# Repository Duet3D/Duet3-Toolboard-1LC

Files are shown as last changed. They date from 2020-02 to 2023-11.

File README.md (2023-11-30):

# Duet-3-Toolboard-1LC
Hardware information for the Duet 3 Toolboard 1LC. This is a CAN-FD connected expansion board for Duet 3 Mainboards:[Duet 3 6HC](https://www.duet3d.com/Duet3Mainboard6HC), [Duet 3 Mini 5+](https://www.duet3d.com/duet3mini5plus) or [Duet 3 6XD](https://www.duet3d.com/duet3mainboard6xd) that is designed to provide complete control for a direct drive extruder. 

Image of Duet 3 Toolboard 1LC

Product page is here: https://www.duet3d.com/Duet3Toolboard1LC

Documentation is here: https://docs.duet3d.com/en/Duet3D_hardware/Duet_3_family/Duet_3_Toolboard_1LC

As always please discuss this on the Duet3d forum: https://forum.duet3d.com/

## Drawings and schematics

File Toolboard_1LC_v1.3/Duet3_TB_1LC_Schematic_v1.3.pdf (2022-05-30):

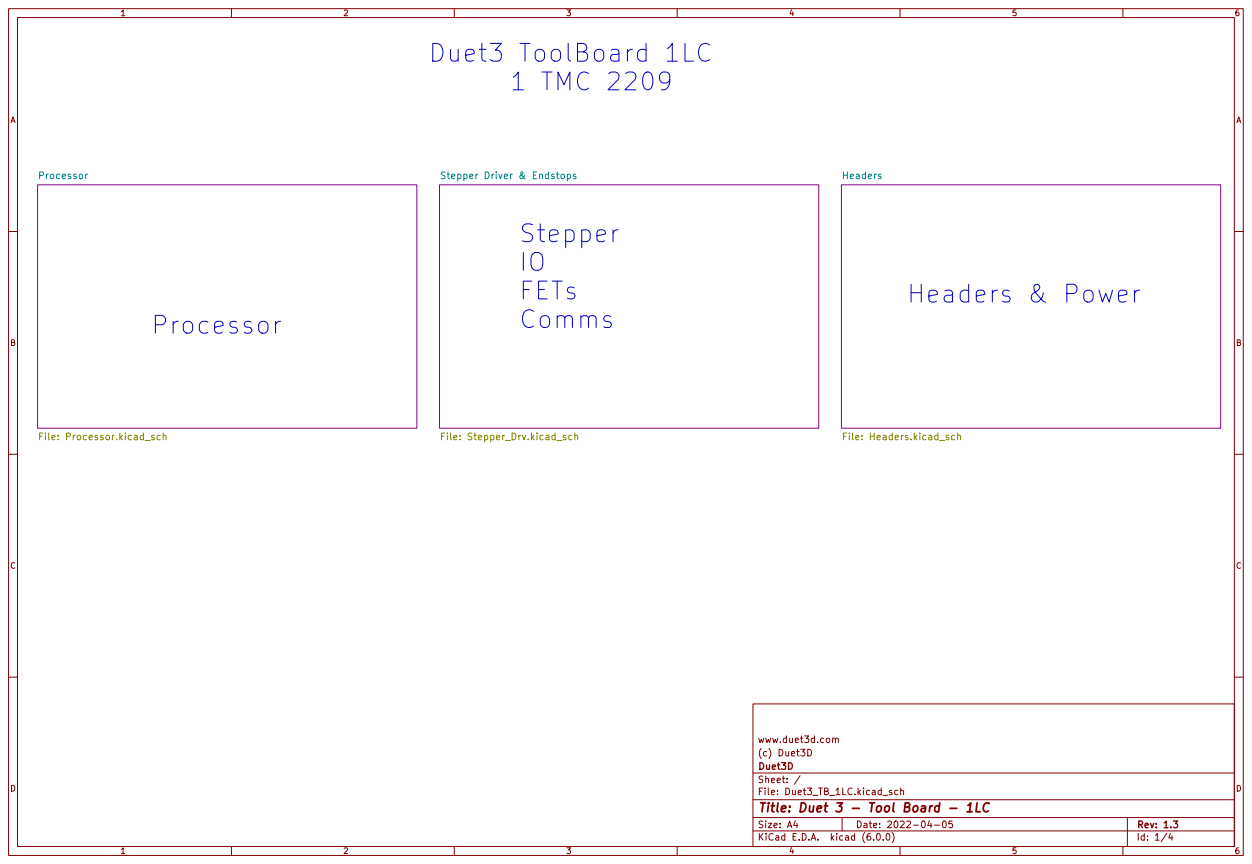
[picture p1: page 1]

Id: 1/4 Title: Duet 3 - Tool Board - 1LC

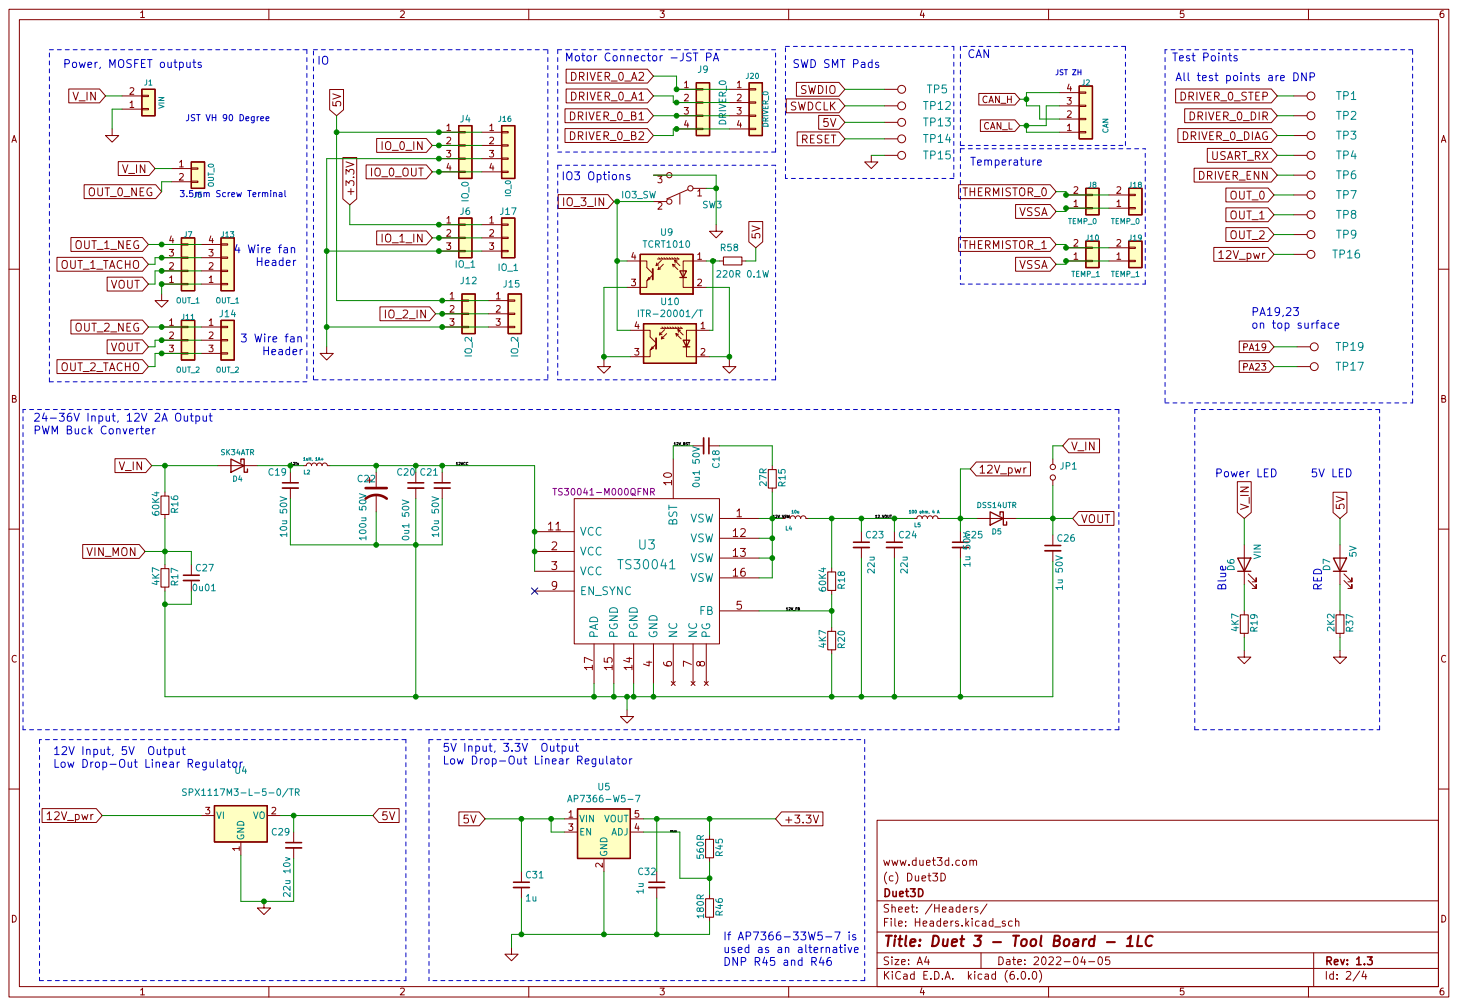
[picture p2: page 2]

12V Input, 5V Output
Low Drop-Out Linear Regulator

5V Input, 3.3V Output

www.duet3d.com
(c) Duet3D
File: Headers.kicad_sch Sheet: /Headers/ Duet3D

Id: 2/4 Title: Duet 3 - Tool Board - 1LC

If AP7366-33W5-7 is used as an alternative DNP R45 and R46

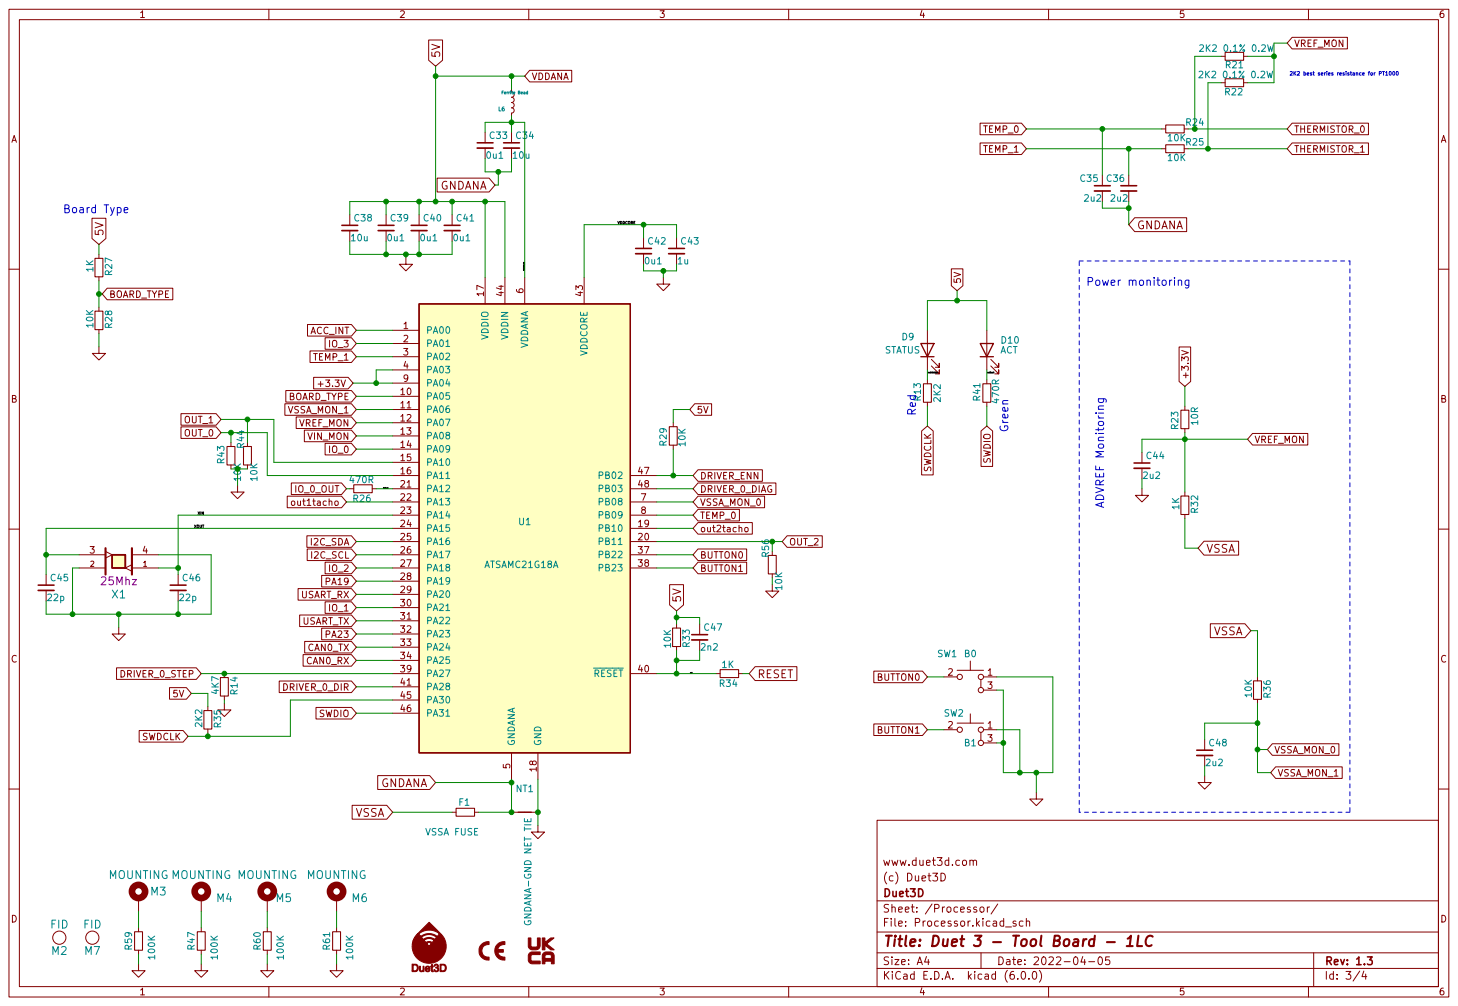
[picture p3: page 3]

2K2 best series resistance for PT1000 ADVREF Monitoring

www.duet3d.com
(c) Duet3D
File: Processor.kicad_sch Sheet: /Processor/ Duet3D

Id: 3/4 Title: Duet 3 - Tool Board - 1LC

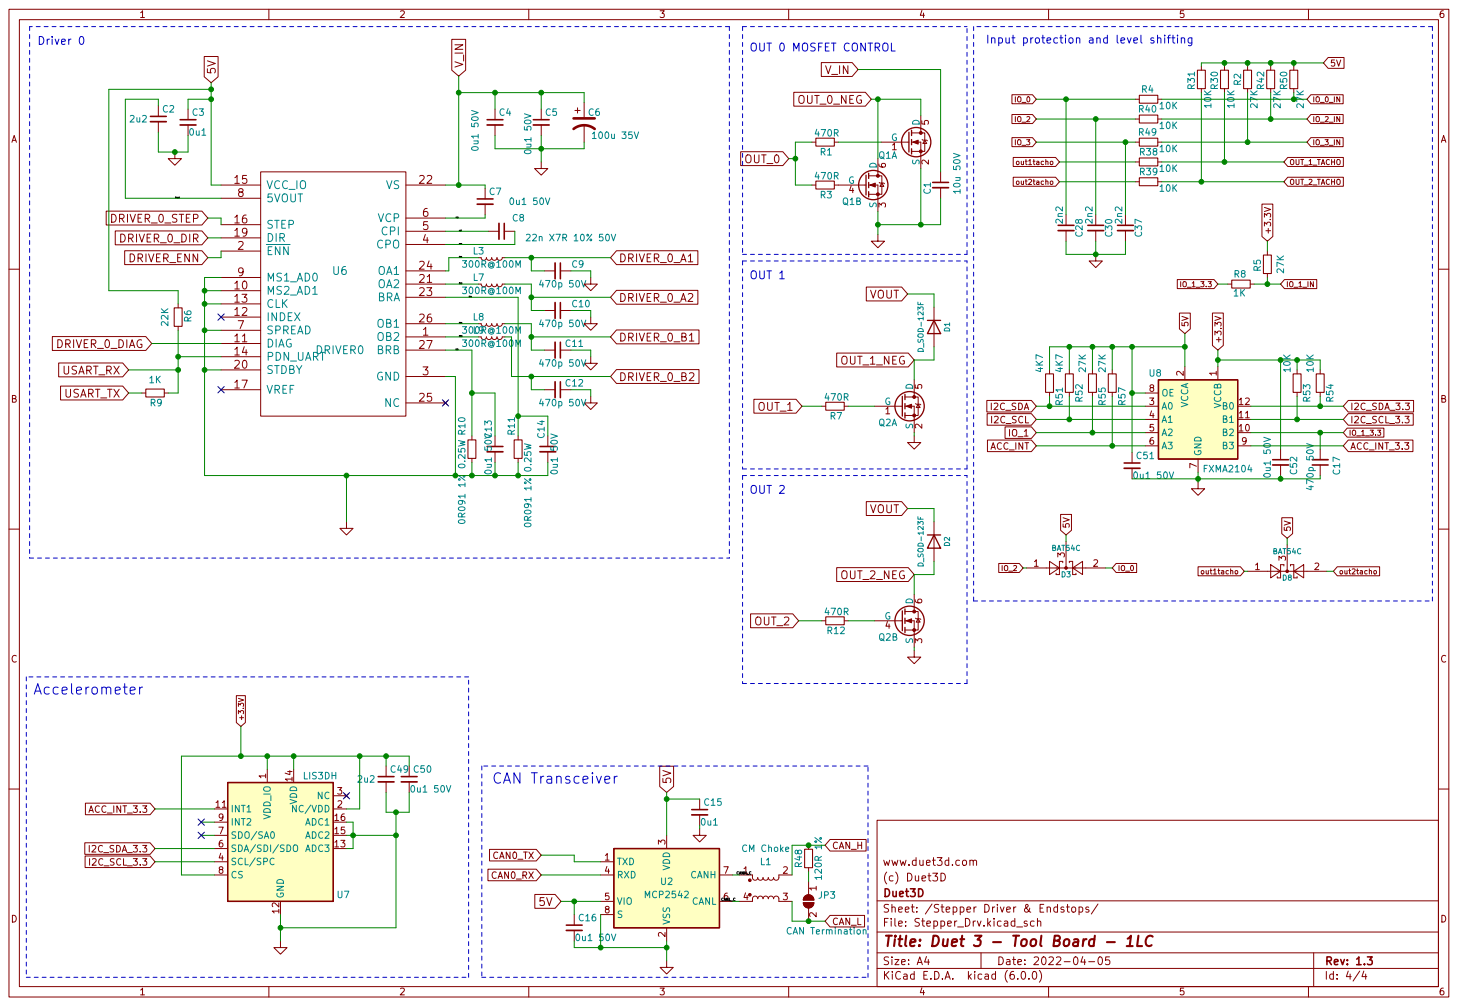
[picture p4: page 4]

Input protection and level shifting

3 RXD 4 VIO 5 CANL 6 CANH 7 S

(c) Duet3D
Sheet: /Stepper Driver & Endstops/ Duet3D

File: Stepper_Drv.kicad_sch
Id: 4/4 Title: Duet 3 - Tool Board - 1LC

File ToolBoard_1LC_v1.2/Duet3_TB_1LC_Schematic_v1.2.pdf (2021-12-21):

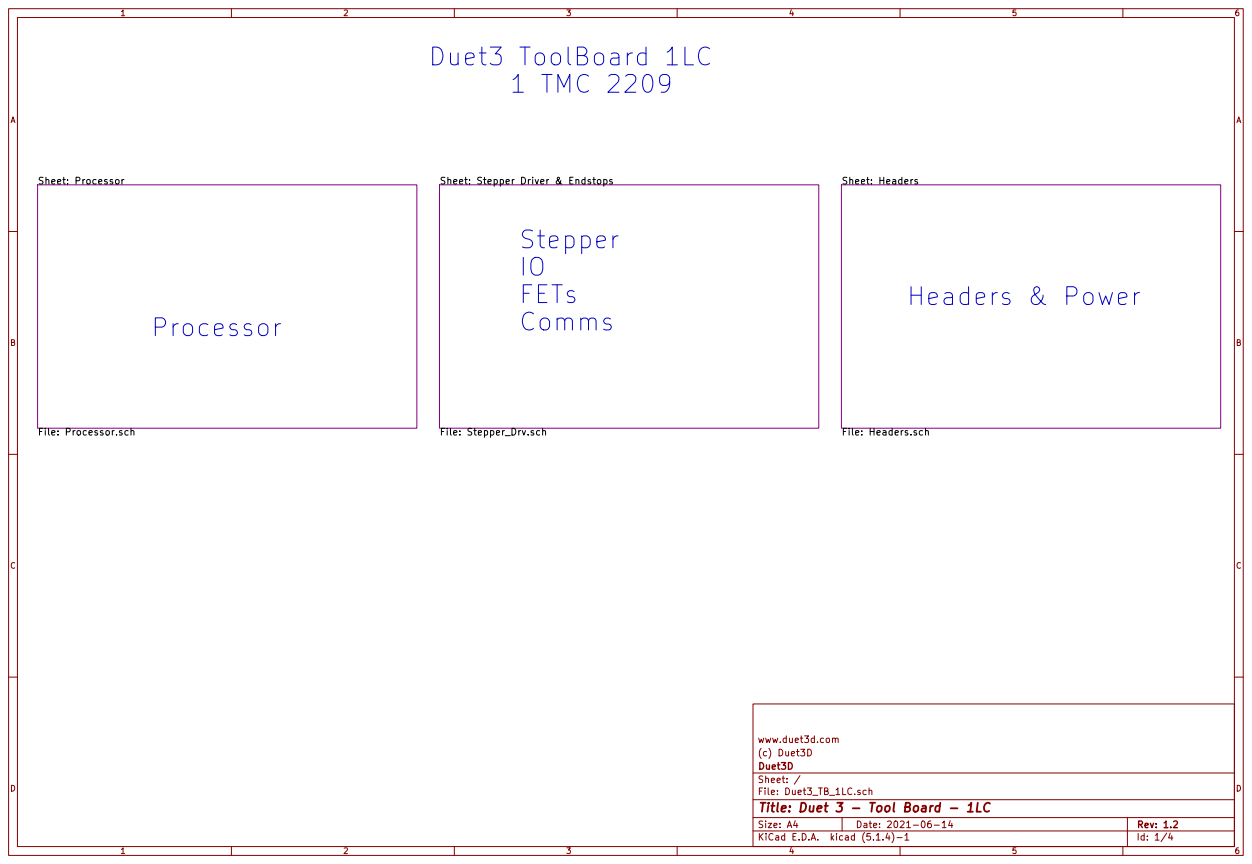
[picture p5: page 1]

Id: 1/4 Title: Duet 3 - Tool Board - 1LC

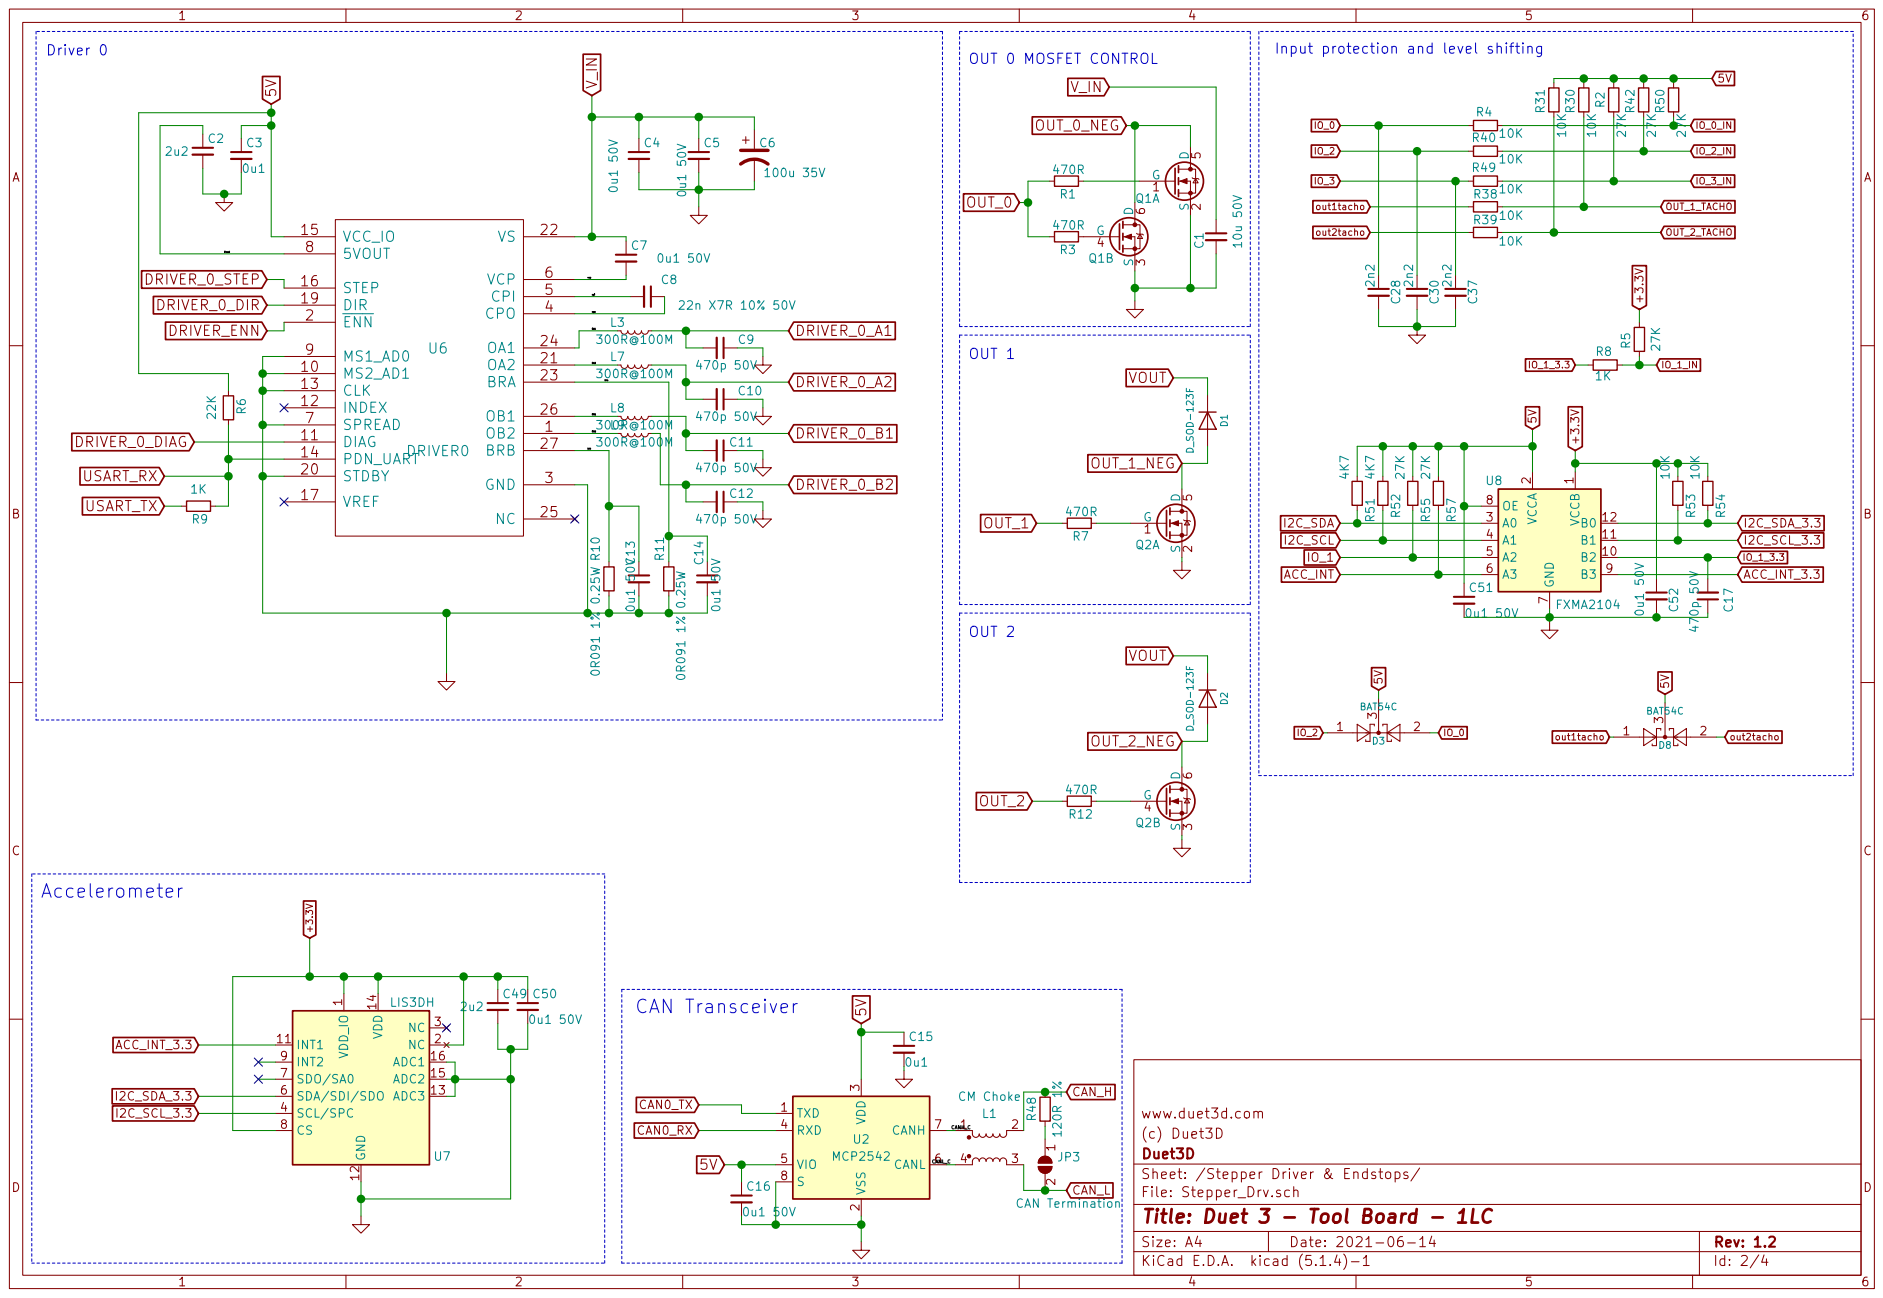
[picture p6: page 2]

3 RXD 4 VIO 5 CANL 6 CANH 7 S

(c) Duet3D
Sheet: /Stepper Driver & Endstops/ Duet3D

File: Stepper_Drv.sch
Id: 2/4 Title: Duet 3 - Tool Board - 1LC

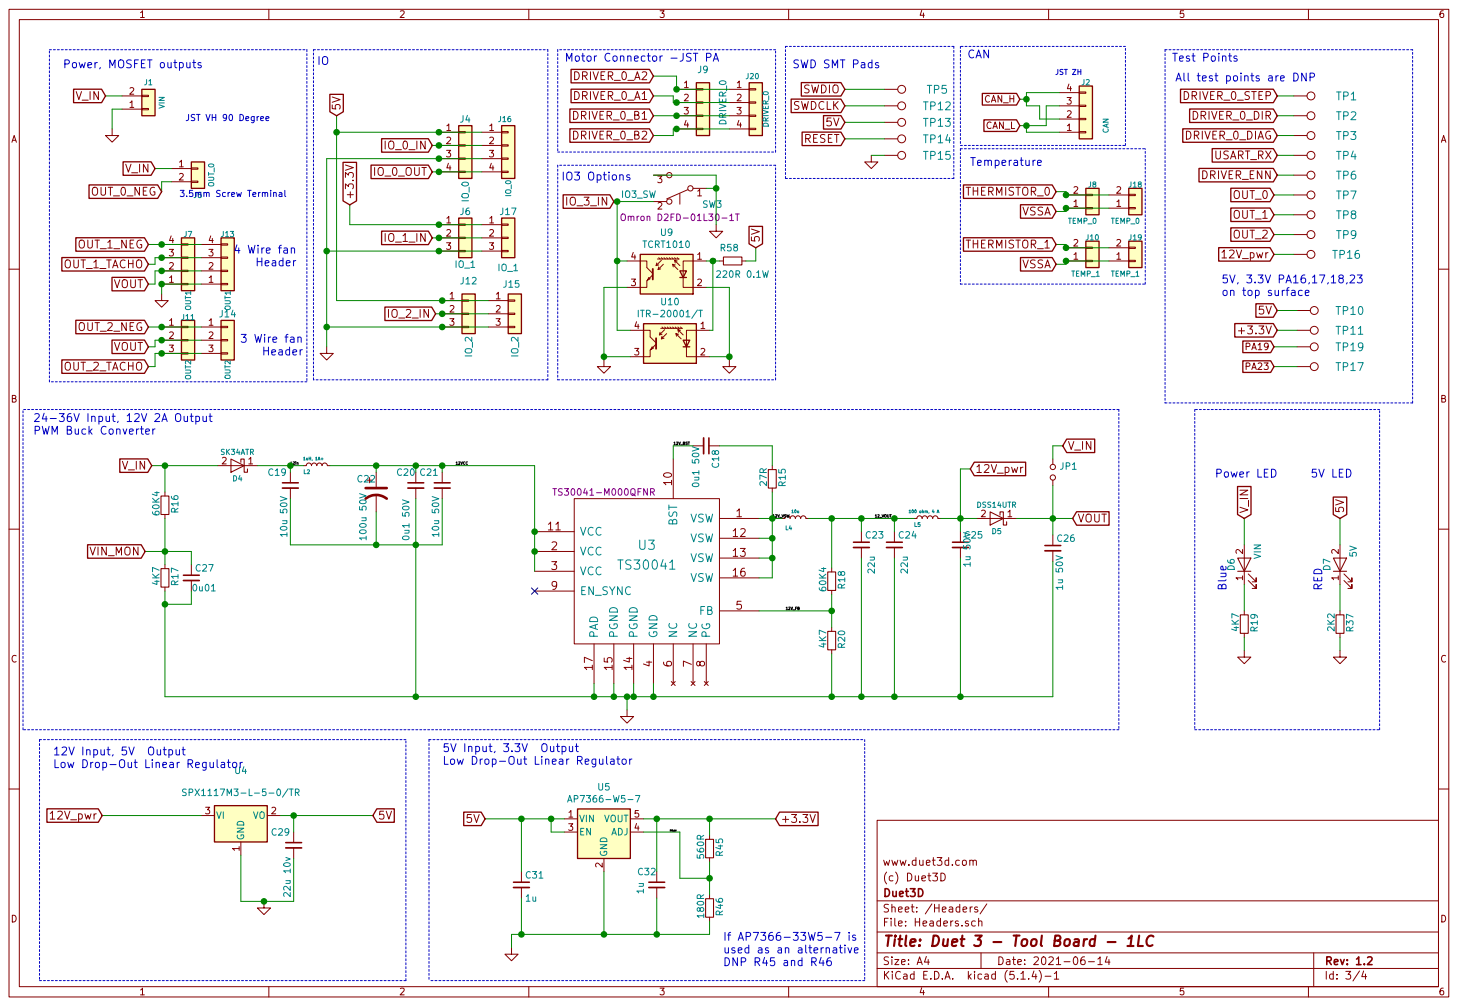
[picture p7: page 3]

12V Input, 5V Output
Low Drop-Out Linear Regulator

5V Input, 3.3V Output

www.duet3d.com
(c) Duet3D
File: Headers.sch Sheet: /Headers/ Duet3D

Id: 3/4 Title: Duet 3 - Tool Board - 1LC

If AP7366-33W5-7 is used as an alternative DNP R45 and R46

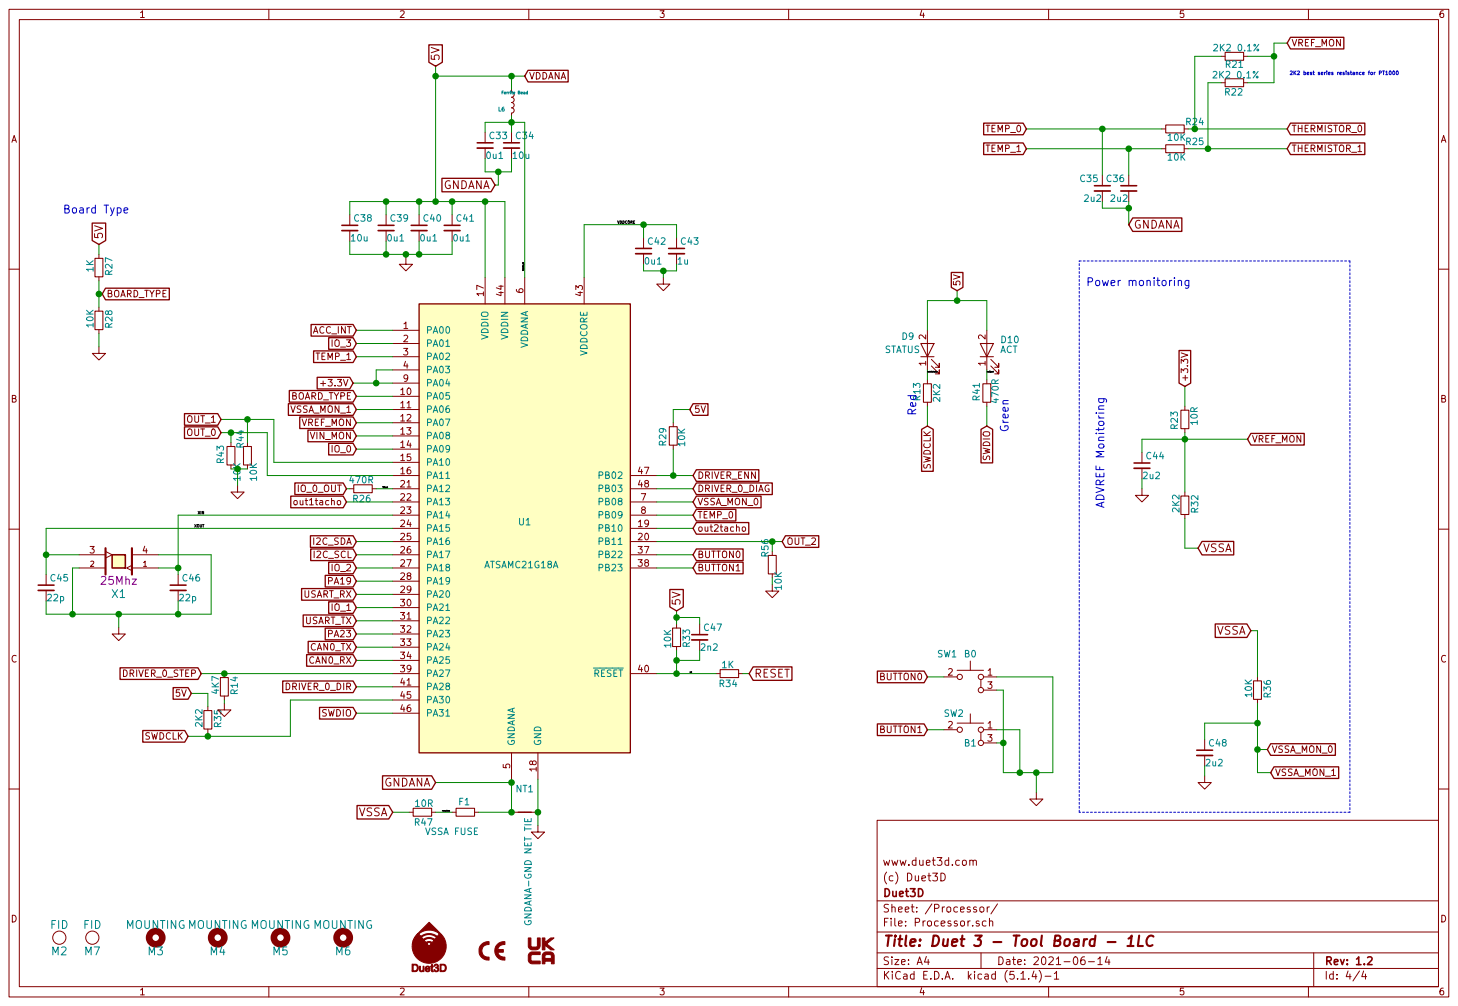
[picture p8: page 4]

www.duet3d.com
(c) Duet3D
File: Processor.sch Sheet: /Processor/ Duet3D

Id: 4/4 Title: Duet 3 - Tool Board - 1LC

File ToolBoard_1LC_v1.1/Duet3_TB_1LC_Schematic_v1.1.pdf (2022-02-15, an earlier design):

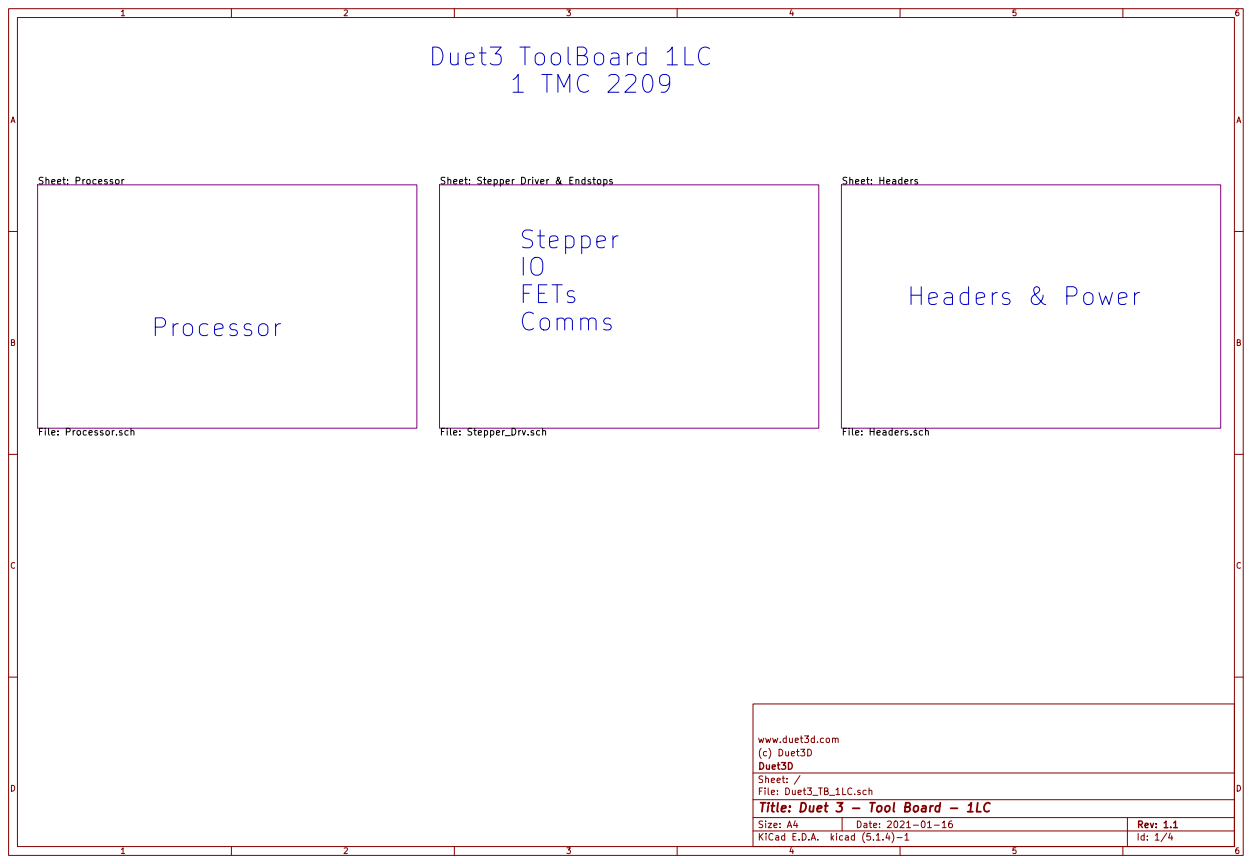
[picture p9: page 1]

Id: 1/4 Title: Duet 3 - Tool Board - 1LC

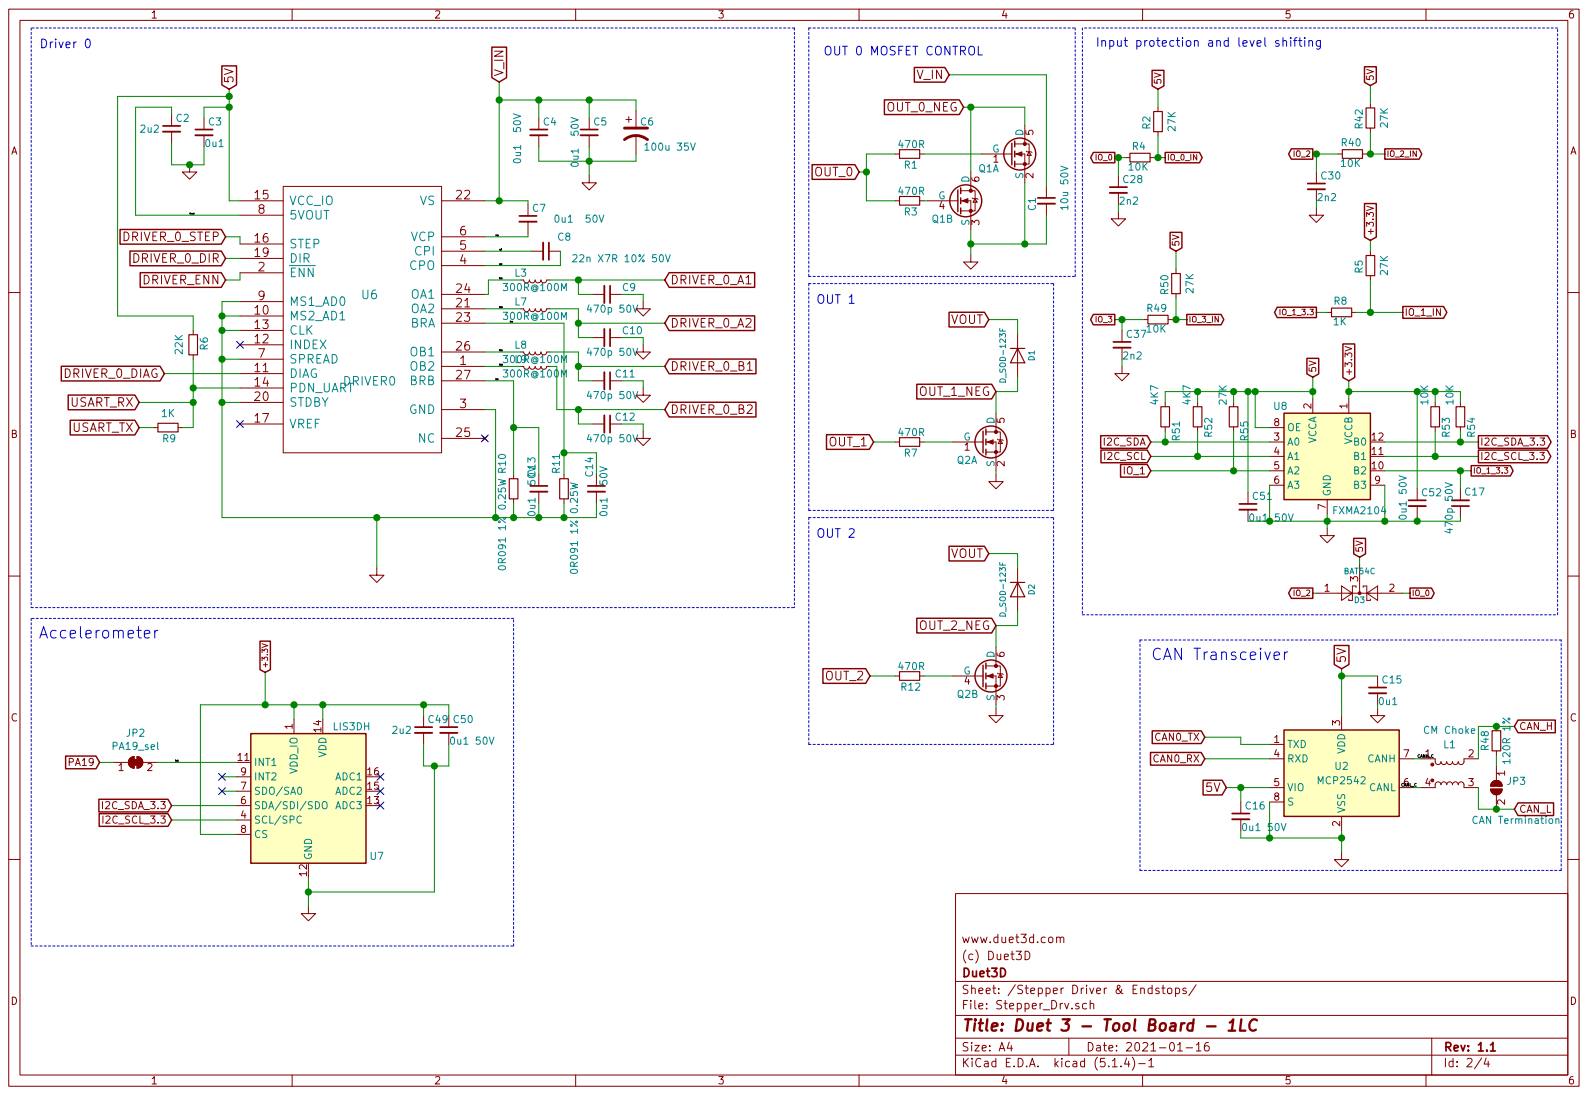
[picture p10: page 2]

CAN Transceiver

LIS3DH

3 RXD 4 VIO 5 CANL 6 CANH 7 S

(c) Duet3D
Sheet: /Stepper Driver & Endstops/ Duet3D

File: Stepper_Drv.sch
Id: 2/4 Title: Duet 3 - Tool Board - 1LC

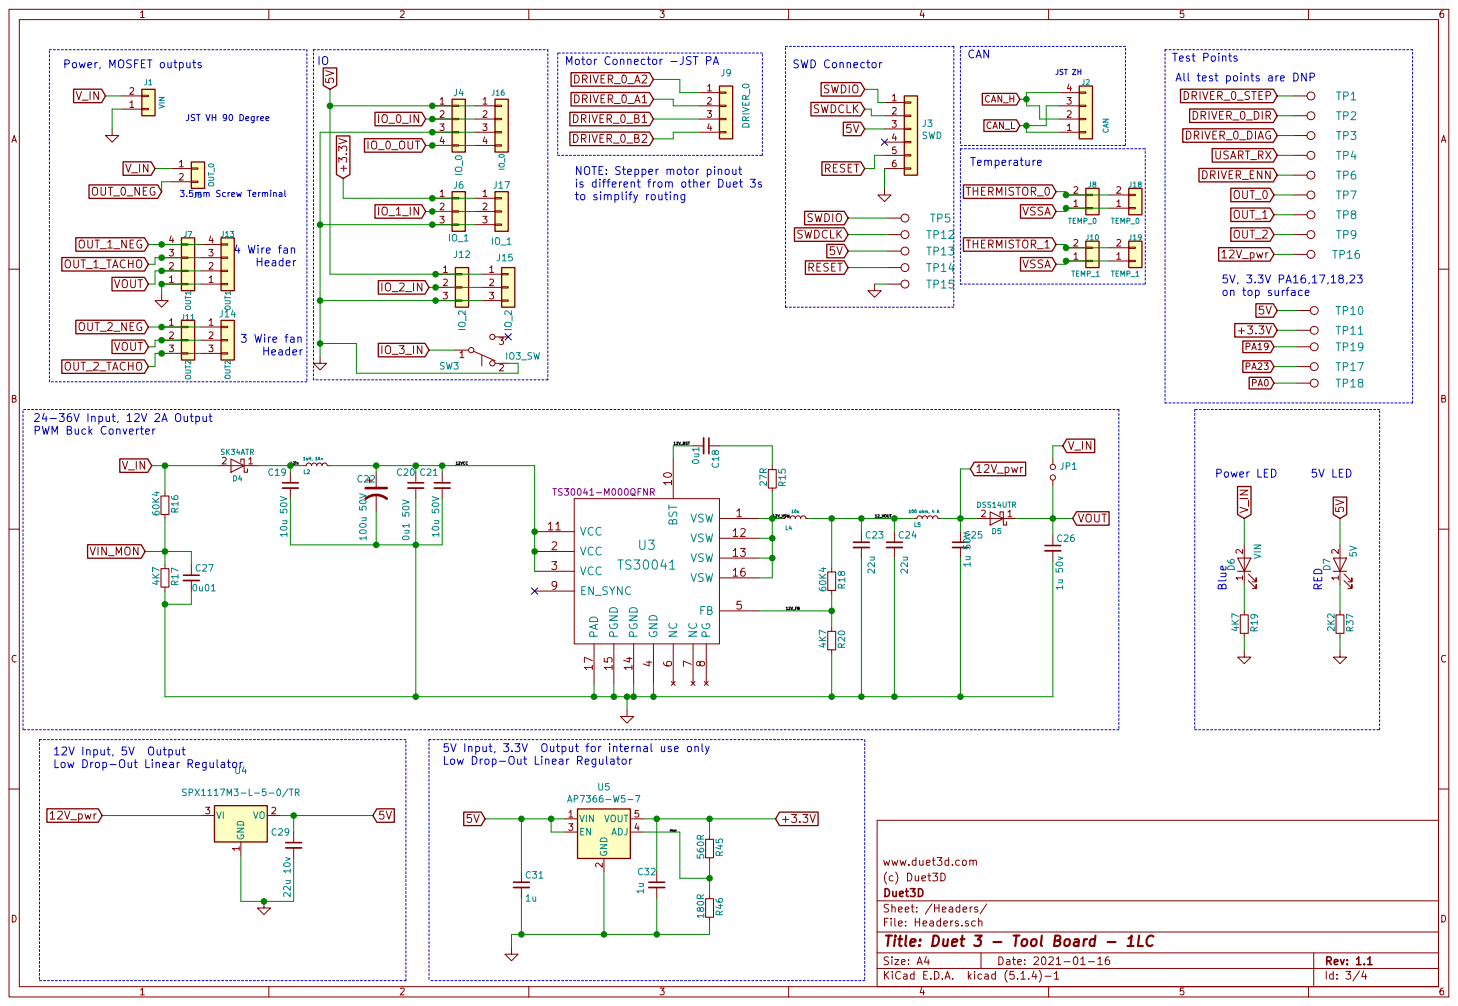
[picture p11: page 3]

is different from other Duet 3s
to simplify routing

3 Wire fan Header 3.5mm Screw Terminal 24-36V Input, 12V 2A Output

5V Input, 3.3V Output for internal use only

1 VO 2 VI 3 U4 SPX1117M3-L-5-0/TR 180R R46 VIN 1 GND

www.duet3d.com
(c) Duet3D
File: Headers.sch Sheet: /Headers/ Duet3D

Id: 3/4 Title: Duet 3 - Tool Board - 1LC

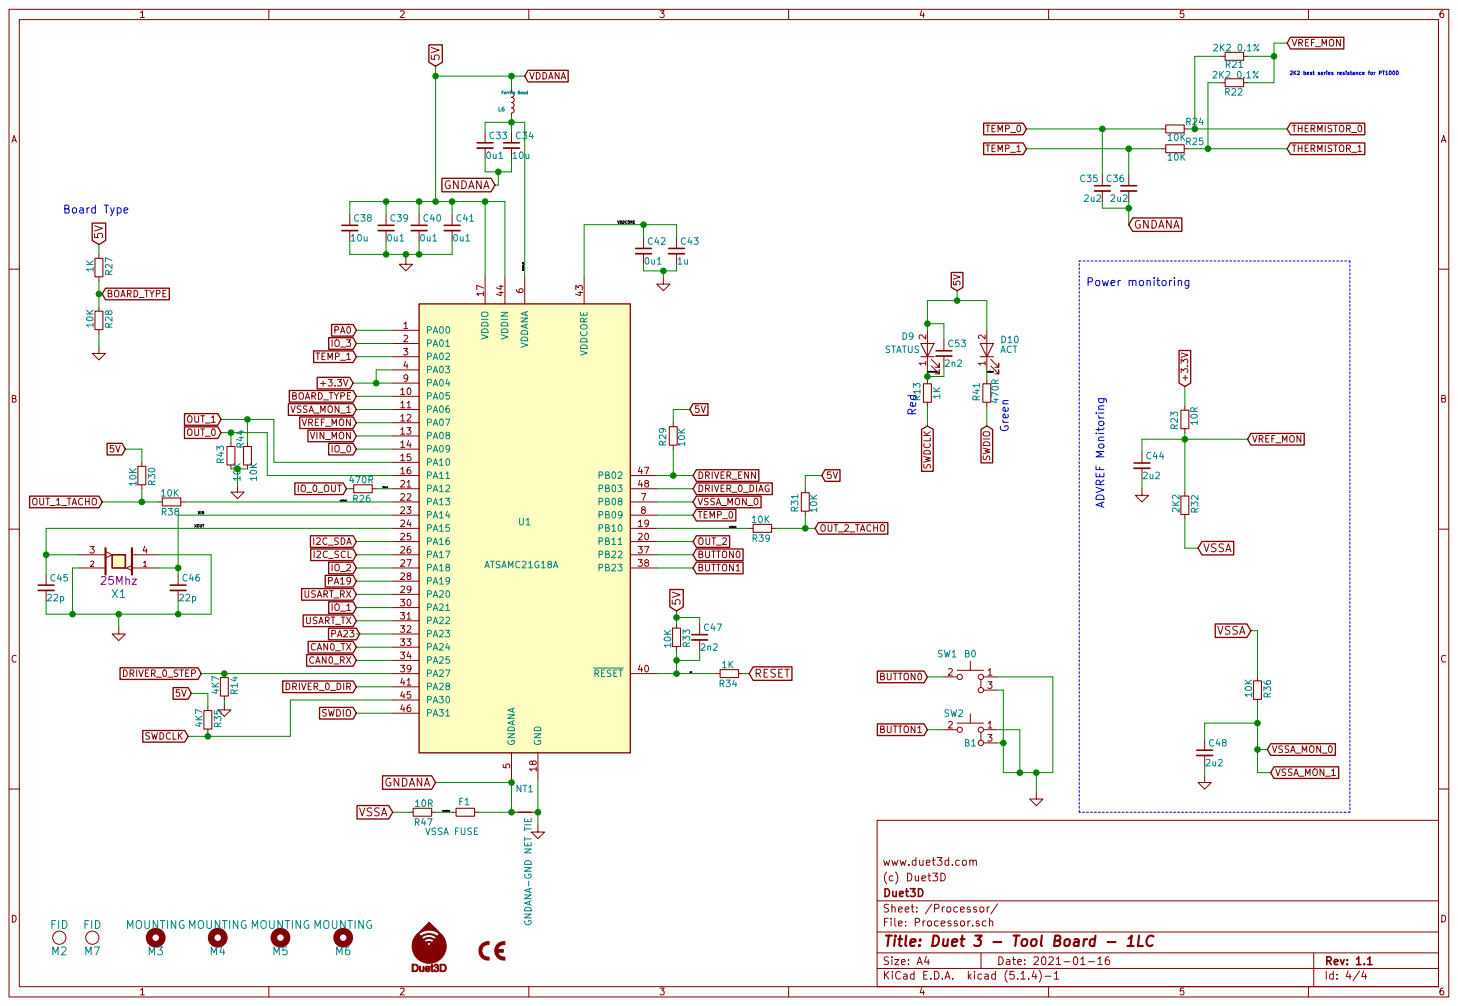
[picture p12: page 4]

2K2 best series resistance for PT1000 ADVREF Monitoring

(c) Duet3D
File: Processor.sch Sheet: /Processor/ Duet3D

Id: 4/4 Title: Duet 3 - Tool Board - 1LC

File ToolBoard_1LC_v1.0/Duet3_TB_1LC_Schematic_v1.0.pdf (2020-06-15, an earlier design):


Id: 1/4 Title: Duet 3 - Tool Board - 1LC


CAN Transceiver

3 RXD 4 VIO 5 CANL 6 CANH 7 S

www.duet3d.com (c) Duet3D Sheet: /Stepper Driver & Endstops/ Duet3D

File: Stepper_Drv.sch
Id: 2/4 Title: Duet 3 - Tool Board - 1LC


All test points are DNP

NOTE: Stepper motor pinout
is different from other Duet 3s
to simplify routing

5V and 3.3V on top surface

5V Input, 3.3V Output for internal use only
Low Drop-Out Linear Regulator

www.duet3d.com
(c) Duet3D
File: Headers.sch Sheet: /Headers/ Duet3D

Id: 3/4 Title: Duet 3 - Tool Board - 1LC


2K2 best series resistance for PT1000

www.duet3d.com
(c) Duet3D
File: Processor.sch Sheet: /Processor/ Duet3D

Id: 4/4 Title: Duet 3 - Tool Board - 1LC

CE not added until tested

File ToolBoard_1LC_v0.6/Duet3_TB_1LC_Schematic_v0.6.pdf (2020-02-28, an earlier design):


License: CERN OHL v1.2 www.duet3d.com

Id: 1/4 Title: Duet 3 - Tool Board - 1LC


CAN Transceiver

3 RXD 4 VIO 5 CANL 6 CANH 7 S

License: CERN OHL v1.2 www.duet3d.com Sheet: /Stepper Driver & Endstops/ Duet3D

File: Stepper_Drv.sch
Id: 2/4 Title: Duet 3 - Tool Board - 1LC


2.54mm Screw Terminal 2.54mm Screw Terminal Power, MOSFET outputs

All test points are DNP

2.54mm Screw Terminal NOTE: Stepper motor pinout

is different from other Duet 3s
to simplify routing

12V Input, 5V Output
Low Drop-Out Linear Regulator

5V Input, 3.3V Output for internal use only

License: CERN OHL v1.2 www.duet3d.com

File: Headers.sch Sheet: /Headers/ Duet3D

Id: 3/4 Title: Duet 3 - Tool Board - 1LC


2K2 best series resistance for PT1000 Board Type

License: CERN OHL v1.2 www.duet3d.com

File: Processor.sch Sheet: /Processor/ Duet3D

Id: 4/4 Title: Duet 3 - Tool Board - 1LC

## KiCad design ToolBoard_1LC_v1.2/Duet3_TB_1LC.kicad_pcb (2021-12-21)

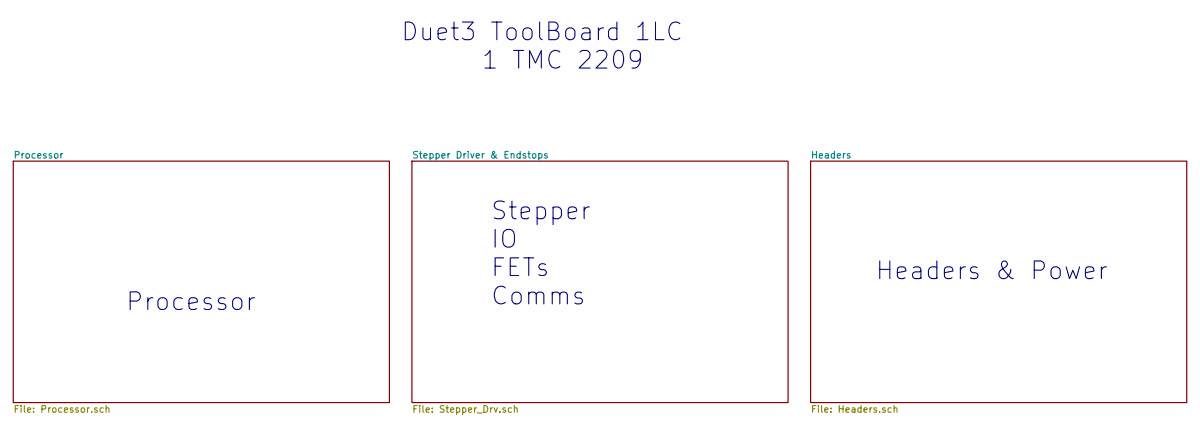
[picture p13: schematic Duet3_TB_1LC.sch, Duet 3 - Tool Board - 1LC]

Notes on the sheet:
Processor
Stepper IO FETs Comms
Headers & Power
Duet3 ToolBoard 1LC 1 TMC 2209

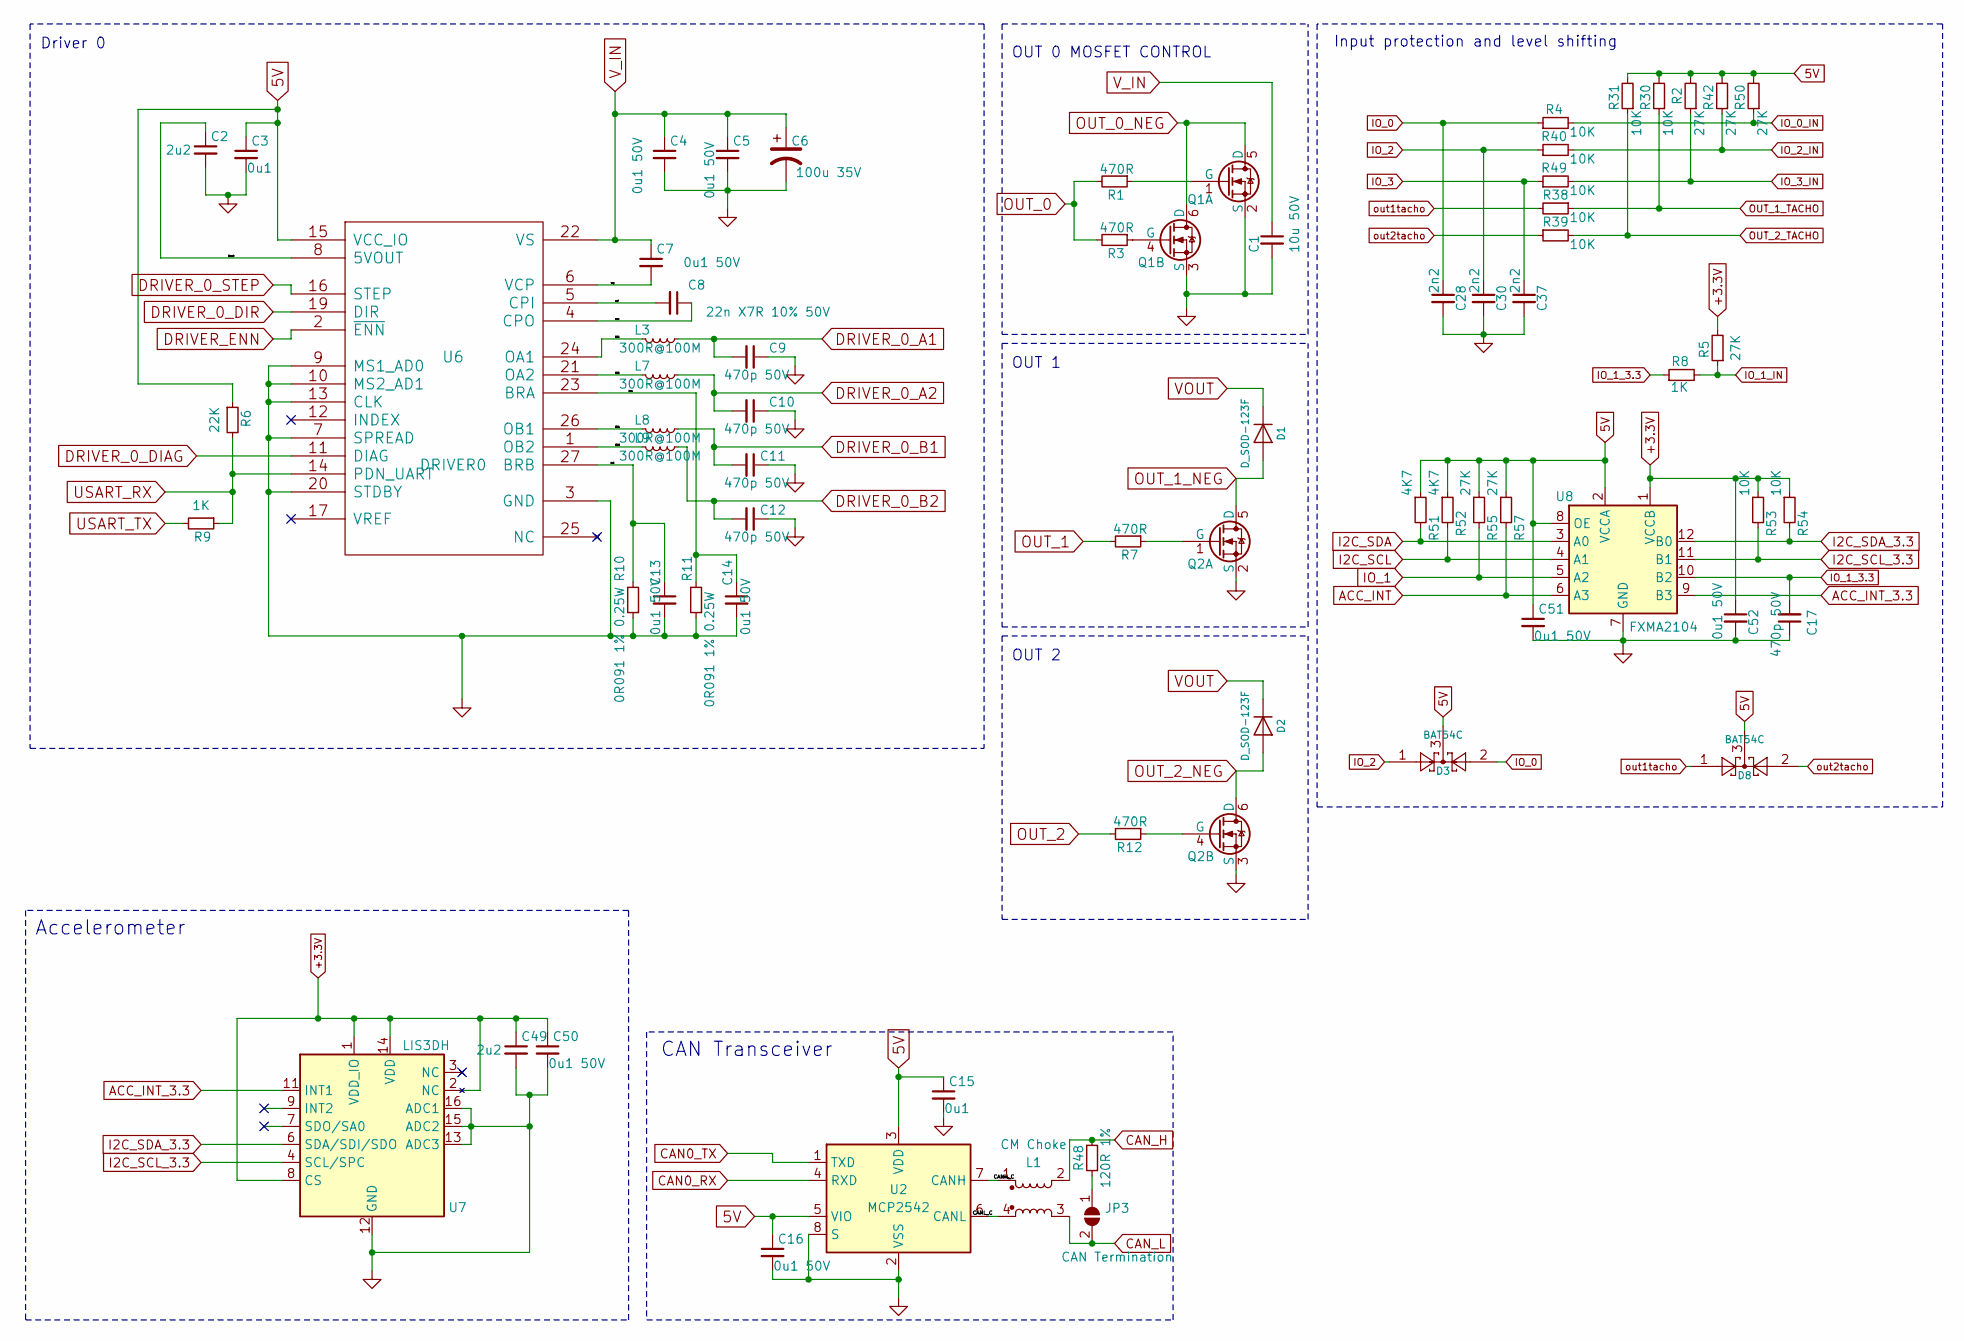
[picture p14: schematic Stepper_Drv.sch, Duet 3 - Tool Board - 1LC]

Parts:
C1: 10u 50V; C_1206_3216Metric; Part Number CL31A106KBHNNNE
C2, C49: 2u2; C_0603_1608Metric_Wbry; Part Number GRM188R6YA225KA12D
C3, C15: 0u1; C_0402_1005Metric_Wbry; Part Number CL05A104KA5NNNC
C4, C5, C7, C13, C14, C16, C50, C51, C52: 0u1 50V; C_0402_1005Metric_Wbry; Part Number GCM155R71H104KE02D
C6: 100u 35V; CP_Elec_6.3x7.7; Part Number 865080545012
C8: 22n X7R 10% 50V; C_0402_1005Metric_Wbry; Part Number CC0402KRX7R9BB223
C9, C10, C11, C12, C17: 470p 50V; C_0402_1005Metric_Wbry; Part Number CC0402KRX7R9BB471
C28, C30, C37: 2n2; C_0402_1005Metric_Wbry; Part Number CC0402KRX7R9BB222 or similar (10v+ is f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
D1, D2: D_SOD-123F; Part Number HS1KFL or equivalent
D3, D8: BAT54C; SOT-23; Part Number BAT54C-7-F/BAT54CLT1G
JP3: CAN Termination; SolderJumper-2_P1.3mm_Open_TrianglePad1.0x1.5mm
L1: CM Choke; Wurth_CM_Choke_744231121; Part Number 744231121 or SRF2012A-121YA
L3, L7, L8, L9: 300R@100M; L_0603_1608Metric; Part Number 742792641 or similar
Q1, Q2: Q_DUAL_NMOS; Fairchild_DualPower33-6_3x3mm-gap; Part Number DMT6018LDR
R1, R3, R7, R12: 470R; R_0402_1005Metric_Wbry; Part Number RK73H1ETTP4700F
R2, R5, R42, R50, R55, R57: 27K; R_0402_1005Metric_Wbry; Part Number RK73H1ETTP2702F
R4, R30, R31, R38, R39, R40, R49: 10K; R_0402_1005Metric_Wbry; Part Number RK73H1ETTP1002F
R6: 22K; R_0402_1005Metric_Wbry; Part Number RK73H1ETTP2202F
R8, R9: 1K; R_0402_1005Metric_Wbry; Part Number RK73H1ETTP1001F
R10, R11: 0R091 1% 0.25W; R_0402_1005Metric_Wbry; Part Number ERJ-2BWFR091X or RLP73M1ER091FTDF
R48: 120R 1%; R_0402_1005Metric_Wbry; Part Number RMCF0402FT120R
R51, R52: 4K7; R_0402_1005Metric_Wbry; Part Number RK73H1ETTP4701F
R53, R54: 10K; R_0402_1005Metric_Wbry; Part Number RK73H1ETTP4701F
U2: MCP2542; DFN-8-1EP_3x2mm_P0.5mm_EP1.3x1.5mm-thinpads; Part Number MCP2542, alternitivelty MCP2558
U6: DRIVER0; QFN-28-1EP_5x5mm_Pitch0.5mm-thinpads; Part Number TMC2209
U7: LIS3DH; Part Number LIS3DHTR
U8: FXMA2104; UMLP-12-1.8x1.8mm_P0.4mm

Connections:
5V: C3.1, C15.1, C16.1, C51.1, D3.3, D8.3, R2.2, R6.1, R30.2, R31.2, R42.2, R50.2, R51.1, R52.1, R55.1, R57.1, U2.3 (VDD), U2.5 (VIO), U6.15 (VCC_IO), U8.2 (VCCA), U8.8 (OE); also elsewhere on the board
+3.3V: C49.1, C50.1, C52.1, R5.2, R53.1, R54.1, U7.1 (VDD_IO), U7.2 (NC), U7.8 (CS), U7.14 (VDD), U8.1 (VCCB); also elsewhere on the board
/Stepper Driver & Endstops/5vout: C2.1, U6.8 (5VOUT)
/Stepper Driver & Endstops/CANH_C: L1.1, U2.7 (CANH)
/Stepper Driver & Endstops/CANL_C: L1.4, U2.6 (CANL)
/Stepper Driver & Endstops/OA1: L3.2, U6.24 (OA1)
/Stepper Driver & Endstops/OA2: L7.2, U6.21 (OA2)
/Stepper Driver & Endstops/OB1: L8.2, U6.26 (OB1)
/Stepper Driver & Endstops/OB2: L9.2, U6.1 (OB2)
/Stepper Driver & Endstops/bra: C14.1, R11.2, U6.23 (BRA)
/Stepper Driver & Endstops/brb: C13.1, R10.2, U6.27 (BRB)
/Stepper Driver & Endstops/cpi: C8.2, U6.5 (CPI)
/Stepper Driver & Endstops/cpo: C8.1, U6.4 (CPO)
/Stepper Driver & Endstops/vcp: C7.2, U6.6 (VCP)
ACC_INT: R57.2, U8.6 (A3); also elsewhere on the board
ACC_INT_3.3: U7.11 (INT1), U8.9 (B3)
CAN0_RX: U2.4 (RXD); also elsewhere on the board
CAN0_TX: U2.1 (TXD); also elsewhere on the board
CAN_H: L1.2, R48.2; also elsewhere on the board
CAN_L: JP3.2 (B), L1.3; also elsewhere on the board
DRIVER_0_A1: C9.2, L3.1; also elsewhere on the board
DRIVER_0_A2: C10.2, L7.1; also elsewhere on the board
DRIVER_0_B1: C11.2, L8.1; also elsewhere on the board
DRIVER_0_B2: C12.2, L9.1; also elsewhere on the board
DRIVER_0_DIAG: U6.11 (DIAG); also elsewhere on the board
DRIVER_0_DIR: U6.19 (DIR); also elsewhere on the board
DRIVER_0_STEP: U6.16 (STEP); also elsewhere on the board
DRIVER_ENN: U6.2 (~ENN); also elsewhere on the board
GND: C1.2, C2.2, C3.2, C4.2, C5.2, C6.2, C9.1, C10.1, C11.1, C12.1, C13.2, C14.2, C15.2, C16.2, C17.1, C28.2, C30.2, C37.2, C49.2, C50.2, C51.2, C52.2, Q1.2 (S), Q1.3 (S), Q2.2 (S), Q2.3 (S), R10.1, R11.1, U2.2 (VSS), U2.8 (S), U2.9 (VSS), U6.3 (GND), U6.7 (SPREAD), U6.9 (MS1_AD0), U6.10 (MS2_AD1), U6.13 (CLK), U6.18 (GND), U6.20 (STDBY), U6.29 (GND), U7.5 (GND), U7.10 (GND), U7.12 (GND), U7.13 (ADC3), U7.15 (ADC2), U7.16 (ADC1), U8.7 (GND); also elsewhere on the board
I2C_SCL: R52.2, U8.4 (A1); also elsewhere on the board
I2C_SCL_3.3: R53.2, U7.4 (SCL/SPC), U8.11 (B1)
I2C_SDA: R51.2, U8.3 (A0); also elsewhere on the board
I2C_SDA_3.3: R54.2, U7.6 (SDA/SDI/SDO), U8.12 (B0)
IO_0: C28.1, D3.2, R4.1; also elsewhere on the board
IO_0_IN: R4.2, R50.1; also elsewhere on the board
IO_1: R55.2, U8.5 (A2); also elsewhere on the board
IO_1_3.3: C17.2, R8.1, U8.10 (B2)
IO_1_IN: R5.1, R8.2; also elsewhere on the board
IO_2: C30.1, D3.1, R40.1; also elsewhere on the board
IO_2_IN: R40.2, R42.1; also elsewhere on the board
IO_3: C37.1, R49.1; also elsewhere on the board
IO_3_IN: R2.1, R49.2; also elsewhere on the board
unnamed: JP3.1 (A), R48.1
unnamed: Q1.1 (G), R1.1
unnamed: Q1.4 (G), R3.1
unnamed: Q2.1 (G), R7.1
unnamed: Q2.4 (G), R12.1
OUT_0: R1.2, R3.2; also elsewhere on the board
OUT_0_NEG: Q1.5 (D), Q1.6 (D); also elsewhere on the board
OUT_1: R7.2; also elsewhere on the board
OUT_1_NEG: D1.2 (A), Q2.5 (D); also elsewhere on the board
OUT_1_TACHO: R30.1, R38.1; also elsewhere on the board
OUT_2: R12.2; also elsewhere on the board
OUT_2_NEG: D2.2 (A), Q2.6 (D); also elsewhere on the board
OUT_2_TACHO: R31.1, R39.2; also elsewhere on the board
USART_RX: R6.2, R9.1, U6.14 (PDN_UART); also elsewhere on the board
USART_TX: R9.2; also elsewhere on the board
VOUT: D1.1 (K), D2.1 (K); also elsewhere on the board
V_IN: C1.1, C4.1, C5.1, C6.1, C7.1, U6.22 (VS), U6.28 (VS); also elsewhere on the board
out1tacho: D8.1, R38.2; also elsewhere on the board
out2tacho: D8.2, R39.1; also elsewhere on the board

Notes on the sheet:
Input protection and level shifting
Driver 0
OUT 1
OUT 0 MOSFET CONTROL
CAN Transceiver
OUT 2
Accelerometer

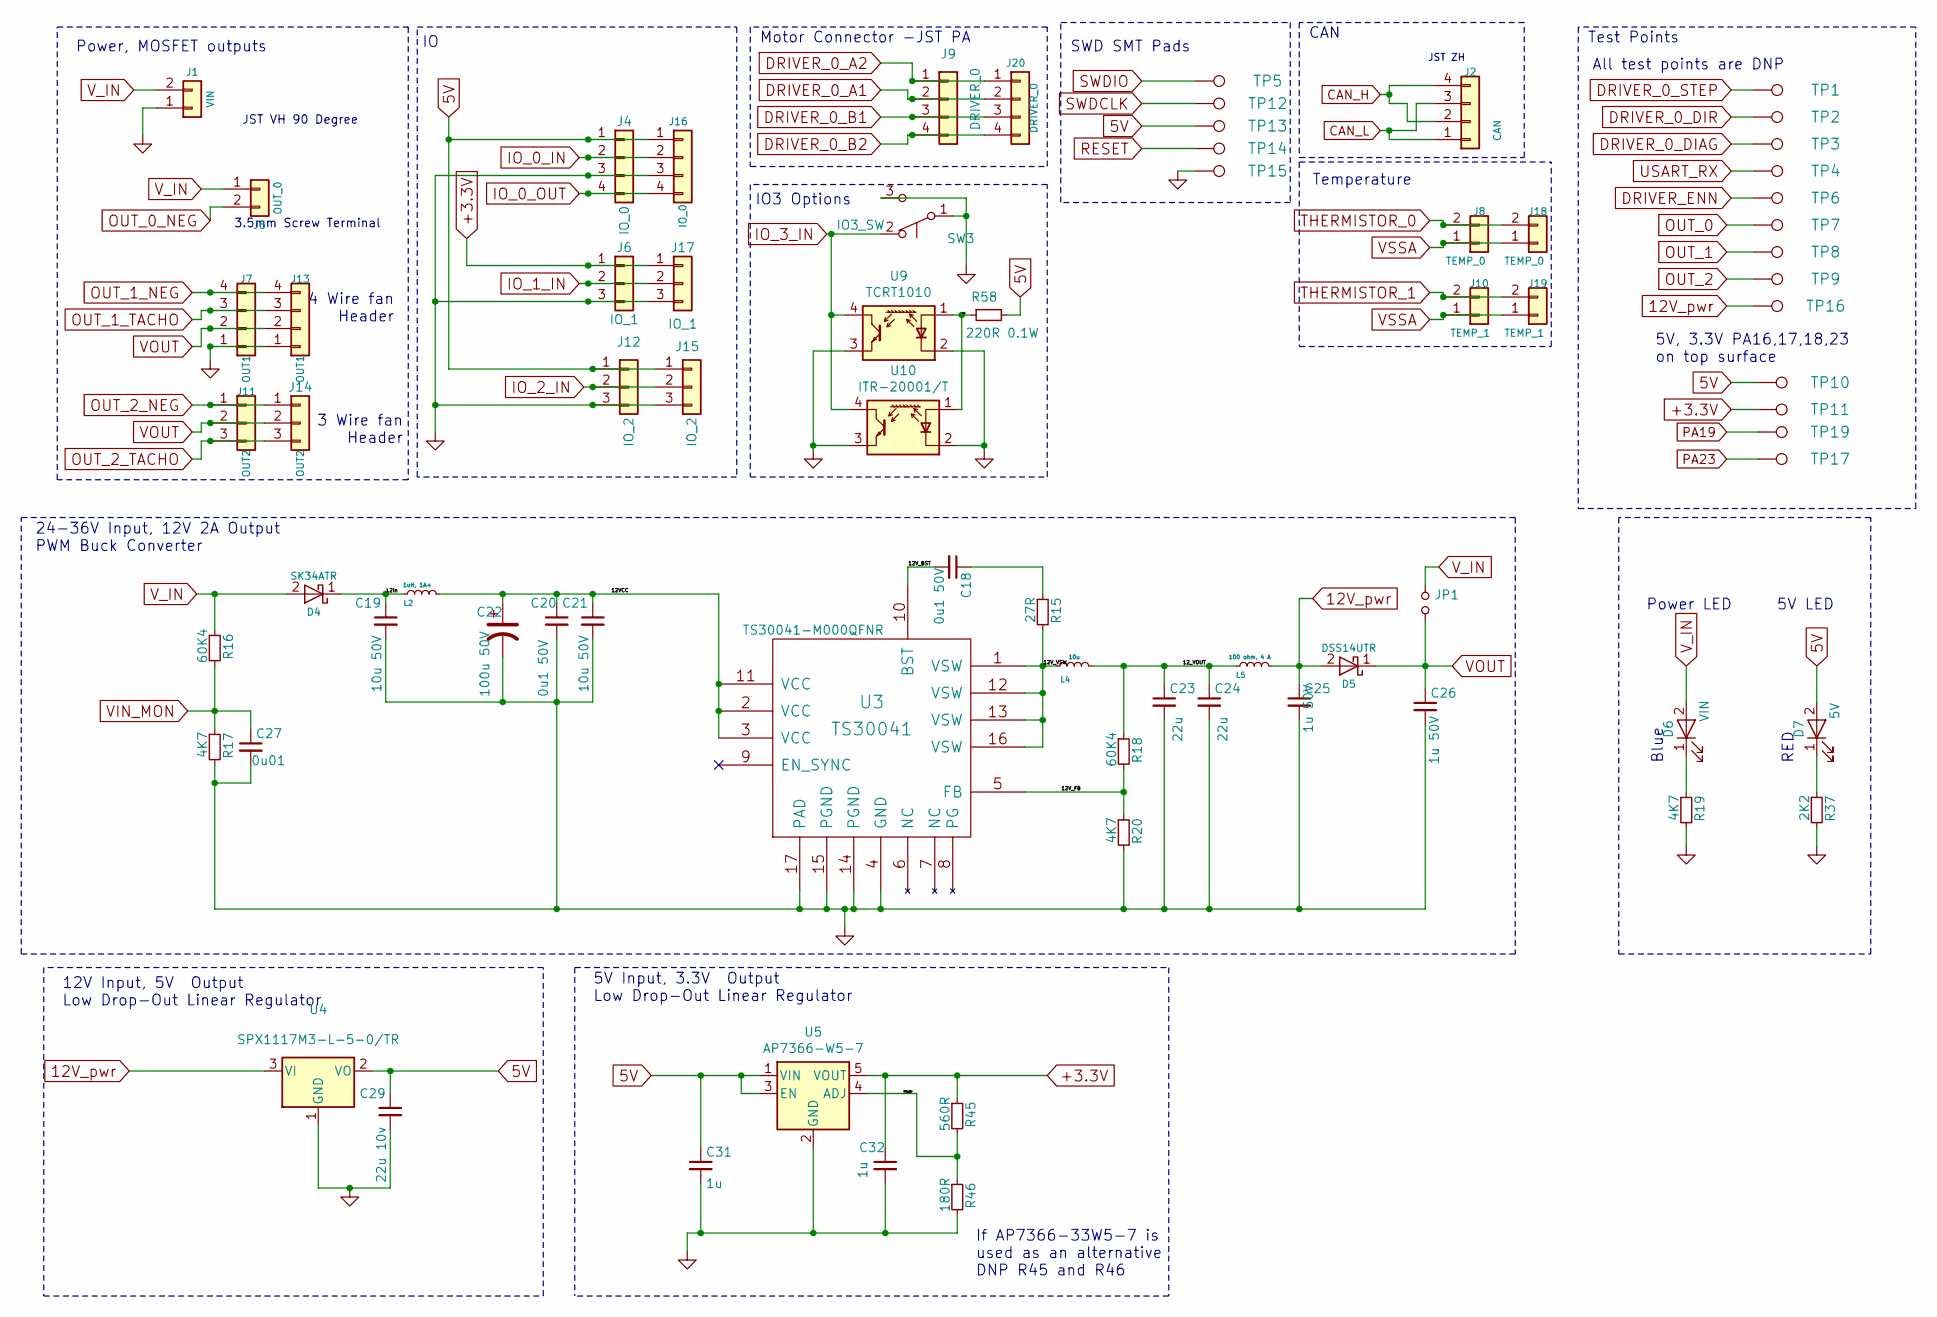
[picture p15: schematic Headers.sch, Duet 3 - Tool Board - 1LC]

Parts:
C18: 0u1 50V; C_0402_1005Metric_Wbry; Part Number CL05A104KA5NNNC
C19, C21: 10u 50V; C_1206_3216Metric; Part Number CL31A106KBHNNNE
C20: 0u1 50V; C_0402_1005Metric_Wbry; Part Number GRM155R61H104JE14D
C22: 100u 50V; CP_Elec_6.3x7.7; Part Number EEE-FTH101XAP
C23, C24: 22u; C_0805_2012Metric; Rating 25V; Part Number GRM21BR61E226ME44L
C25, C26: 1u 50V; C_0603_1608Metric_Wbry; Part Number CL10A105KB8NNNC
C27: 0u01; C_0402_1005Metric_Wbry; Part Number TMK105B7103KV-F
C29: 22u 10v; C_0805_2012Metric; Part Number GRM21BR61A226ME51L or equivalent
C31, C32: 1u; C_0603_1608Metric_Wbry; Part Number CL10A105KA8NNNC
D4: SK34ATR; D_SMA; Rating 1A+ 40V+; Part Number SK34ATR or similar SMA footprint
D5: DSS14UTR; D_SOD-123F; Rating 1A,40V; Part Number DSS14UTR or RB162MM-40TR or similar
D6: VIN; LED_0603_1608Metric; Part Number 150060BS75000 or equivalent Blue
D7: 5V; LED_0603_1608Metric; Part Number 150060RS75000 or equivalent Red
J1: VIN; JST_VH_B2PS-VH_1x02_P3.96mm_Short_Horizontal; Part Number B2PS-VH(LF)(SN)
J2: CAN; JST_ZH_S4B-ZH_1x04_P1.50mm_Horizontal; Part Number S4B-ZR(LF)(SN)
J4: IO_0; JST_PH_S4B-PH-K_1x04_P2.00mm_Horizontal; Part Number S4B-PH-K-S(LF)(SN)
J5: OUT_0; 3.5MM_2X1; Part Number Kaifeng KF128L-3.50-2
J6: IO_1; JST_PH_S3B-PH-K_1x03_P2.00mm_Horizontal; Part Number S3B-PH-K-S(LF)(SN)
J7: OUT1; JST_PH_S4B-PH-K_1x04_P2.00mm_Horizontal; Part Number S4B-PH-K-S(LF)(SN)
J8: TEMP_0; JST_PH_S2B-PH-K_1x02_P2.00mm_Horizontal; Part Number S2B-PH-K-S(LF)(SN)
J9: DRIVER_0; JST_PH_S4B-PH-K_1x04_P2.00mm_Horizontal; Part Number S4B-PH-K-S(LF)(SN)
J10: TEMP_1; JST_PH_S2B-PH-K_1x02_P2.00mm_Horizontal; Part Number S2B-PH-K-S(LF)(SN)
J11: OUT2; JST_PH_S3B-PH-K_1x03_P2.00mm_Horizontal; Part Number S3B-PH-K-S(LF)(SN)
J12: IO_2; JST_PH_S3B-PH-K_1x03_P2.00mm_Horizontal; Part Number S3B-PH-K-S(LF)(SN)
J13: OUT1; TerminalBlock_TE_282834-4_1x04_P2.54mm_Horizontal; Part Number - DNP
J14: OUT2; TerminalBlock_TE_282834-3_1x03_P2.54mm_Horizontal; Part Number - DNP
J15: IO_2; TerminalBlock_TE_282834-3_1x03_P2.54mm_Horizontal; Part Number DNP
J16: IO_0; TerminalBlock_TE_282834-4_1x04_P2.54mm_Horizontal; Part Number - DNP
J17: IO_1; TerminalBlock_TE_282834-3_1x03_P2.54mm_Horizontal; Part Number - DNP
J18: TEMP_0; TerminalBlock_Valcon_MB312-2.54-02_P2.54mm_Horizontal; Part Number MB312-2.54-02_P2.54mm - DNP
J19: TEMP_1; TerminalBlock_Valcon_MB312-2.54-02_P2.54mm_Horizontal; Part Number MB312-2.54-02_P2.54mm - DNP
J20: DRIVER_0; TerminalBlock_TE_282834-4_1x04_P2.54mm_Horizontal; Part Number - DNP
JP1: V_OUT JMP; PinHeader_1x02_P2.54mm_Vertical
L2: 1uH, 1A+; L_1008_2512Metric; Part Number MGV2520101R0M-10 or similar 1008 footpr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
L4: 10u; L_Wuerth_7440405xxxx; Part Number 74404054100 or NR5040T100M
L5: 100 ohm, 4 A; L_0805_2012Metric; Part Number MPZ2012S101A or similar
R15: 27R; R_0402_1005Metric_Wbry; Rating 0.1W+; Part Number RC0402FR-0727RL
R16, R18: 60K4; R_0402_1005Metric_Wbry; Part Number ERJ-2RKF6042X
R17, R19, R20: 4K7; R_0402_1005Metric_Wbry; Part Number RK73H1ETTP4701F
R37: 2K2; R_0402_1005Metric_Wbry; Part Number RK73H1ETTP2201F
R45: 560R; R_0402_1005Metric_Wbry; Part Number RMCF0402FT560R
R46: 180R; R_0402_1005Metric_Wbry; Part Number RMCF0402FT180R
R58: 220R 0.1W; R_0402_1005Metric_Wbry; Part Number RK73H1ETTP2200F
SW3: IO3_SW; Ultra_Subminiature_Switch-SPDT; Part Number DNP - Omron D2FD-1L30-1T
TP1: STEP; TestPoint_Pad_D1.5mm; Part Number virtual component - DNP
TP2: DIR; TestPoint_Pad_D1.5mm; Part Number virtual component - DNP
TP3: DIAG; TestPoint_Pad_D1.5mm; Part Number virtual component - DNP
TP4: U_RX; TestPoint_Pad_D1.5mm; Part Number virtual component - DNP
TP5: SWDIO; TestPoint_Pad_D1.5mm; Part Number virtual component - DNP
TP6: ENN; TestPoint_Pad_D1.5mm; Part Number virtual component - DNP
TP7: OUT_0; TestPoint_Pad_D1.5mm; Part Number virtual component - DNP
TP8: OUT_1; TestPoint_Pad_D1.5mm; Part Number virtual component - DNP
TP9: OUT_2; TestPoint_Pad_D1.5mm; Part Number virtual component - DNP
TP10, TP13: 5V; TestPoint_Pad_D1.5mm; Part Number virtual component - DNP
TP11: 3.3V; TestPoint_Pad_D1.5mm; Part Number virtual component - DNP
TP12: SWDCLK; TestPoint_Pad_D1.5mm; Part Number virtual component - DNP
TP14: RESET; TestPoint_Pad_D1.5mm; Part Number virtual component - DNP
TP15: GND; TestPoint_Pad_D1.5mm; Part Number virtual component - DNP
TP16: 12V_pwr; TestPoint_Pad_D1.5mm; Part Number virtual component - DNP
TP17: PA23; TestPoint_Pad_D1.5mm; Part Number virtual component - DNP
TP19: PA19; TestPoint_Pad_D1.5mm; Part Number virtual component - DNP
U3: TS30041; QFN-16-1EP_3x3mm_P0.5mm_EP1.8x1.8mm-thinpads; Rating Adj (set to 12V) 1A; Part Number TS30041-M000QFNR
U4: SPX1117M3-L-5-0/TR; SOT-223-3_TabPin2; Part Number SPX1117M3-L-5-0/TR
U5: AP7366-W5-7; SOT-23-5; Part Number AP7366-W5-7 (If AP7366-33W5-7 is used a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
U9: TCRT1010; Vishay_TCRT1010; Part Number DNP
U10: ITR-20001/T; ITR-20001_T; Part Number DNP

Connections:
5V: C29.1, C31.1, D7.2 (A), J4.1, J12.1, J15.1, J16.1, R58.2, TP10.1, TP13.1, U4.2 (VO), U5.1 (VIN), U5.3 (EN); also elsewhere on the board
12V_pwr: C25.1, D5.2 (A), L5.2, TP16.1, U4.3 (VI)
+3.3V: C32.1, J6.1, J17.1, R45.1, TP11.1, U5.5 (VOUT); also elsewhere on the board
/Headers/3V3_ADJ: R45.2, R46.1, U5.4 (ADJ)
/Headers/12VCC: C20.1, C21.1, C22.1, L2.2, U3.2 (VCC), U3.3 (VCC), U3.11 (VCC)
/Headers/12V_BST: C18.2, U3.10 (BST)
/Headers/12V_FB: R18.2, R20.1, U3.5 (FB)
/Headers/12V_VSW: L4.1, R15.2, U3.1 (VSW), U3.12 (VSW), U3.13 (VSW), U3.16 (VSW)
/Headers/12_VOUT: C23.1, C24.1, L4.2, L5.1, R18.1
/Headers/L2in: C19.1, D4.1 (K), L2.1
/Headers/col: R58.1, U9.1 (A), U10.1 (A)
CAN_H: J2.2, J2.4; also elsewhere on the board
CAN_L: J2.1, J2.3; also elsewhere on the board
DRIVER_0_A1: J9.2, J20.2; also elsewhere on the board
DRIVER_0_A2: J9.1, J20.1; also elsewhere on the board
DRIVER_0_B1: J9.3, J20.3; also elsewhere on the board
DRIVER_0_B2: J9.4, J20.4; also elsewhere on the board
DRIVER_0_DIAG: TP3.1; also elsewhere on the board
DRIVER_0_DIR: TP2.1; also elsewhere on the board
DRIVER_0_STEP: TP1.1; also elsewhere on the board
DRIVER_ENN: TP6.1; also elsewhere on the board
GND: C19.2, C20.2, C21.2, C22.2, C23.2, C24.2, C25.2, C26.2, C27.2, C29.2, C31.2, C32.2, J1.1, J4.3, J6.3, J7.1, J12.3, J13.1, J15.3, J16.3, J17.3, R17.2, R19.2, R20.2, R37.2, R46.2, SW3.1 (B), SW3.3 (C), TP15.1, U3.4 (GND), U3.14 (PGND), U3.15 (PGND), U3.17 (PAD), U4.1 (GND), U5.2 (GND), U9.2 (K), U9.3 (E), U10.2 (K), U10.3 (E); also elsewhere on the board
IO_0_IN: J4.2, J16.2; also elsewhere on the board
IO_0_OUT: J4.4, J16.4; also elsewhere on the board
IO_1_IN: J6.2, J17.2; also elsewhere on the board
IO_2_IN: J12.2, J15.2; also elsewhere on the board
IO_3_IN: SW3.2 (A), U9.4 (C), U10.4 (C); also elsewhere on the board
unnamed: C18.1, R15.1
unnamed: D6.1 (K), R19.1
unnamed: D7.1 (K), R37.1
OUT_0: TP7.1; also elsewhere on the board
OUT_0_NEG: J5.2; also elsewhere on the board
OUT_1: TP8.1; also elsewhere on the board
OUT_1_NEG: J7.4, J13.4; also elsewhere on the board
OUT_1_TACHO: J7.3, J13.3; also elsewhere on the board
OUT_2: TP9.1; also elsewhere on the board
OUT_2_NEG: J11.1, J14.1; also elsewhere on the board
OUT_2_TACHO: J11.3, J14.3; also elsewhere on the board
PA19: TP19.1; also elsewhere on the board
PA23: TP17.1; also elsewhere on the board
RESET: TP14.1; also elsewhere on the board
SWDCLK: TP12.1; also elsewhere on the board
SWDIO: TP5.1; also elsewhere on the board
THERMISTOR_0: J8.2, J18.2; also elsewhere on the board
THERMISTOR_1: J10.2, J19.2; also elsewhere on the board
USART_RX: TP4.1; also elsewhere on the board
VIN_MON: C27.1, R16.2, R17.1; also elsewhere on the board
VOUT: C26.1, D5.1 (K), J7.2, J11.2, J13.2, J14.2, JP1.2; also elsewhere on the board
VSSA: J8.1, J10.1, J18.1, J19.1; also elsewhere on the board
V_IN: D4.2 (A), D6.2 (A), J1.2, J5.1, JP1.1, R16.1; also elsewhere on the board

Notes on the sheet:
Power, MOSFET outputs
Temperature
Motor Connector -JST PA
Test Points
All test points are DNP
CAN
SWD SMT Pads
4 Wire fan Header
5V, 3.3V PA16,17,18,23 on top surface
5V Input, 3.3V Output Low Drop-Out Linear Regulator
Power LED
Blue
12V Input, 5V Output Low Drop-Out Linear Regulator
24-36V Input, 12V 2A Output PWM Buck Converter
3.5mm Screw Terminal
3 Wire fan Header
5V LED
RED
JST VH 90 Degree
JST ZH
IO3 Options
If AP7366-33W5-7 is used as an alternative DNP R45 and R46

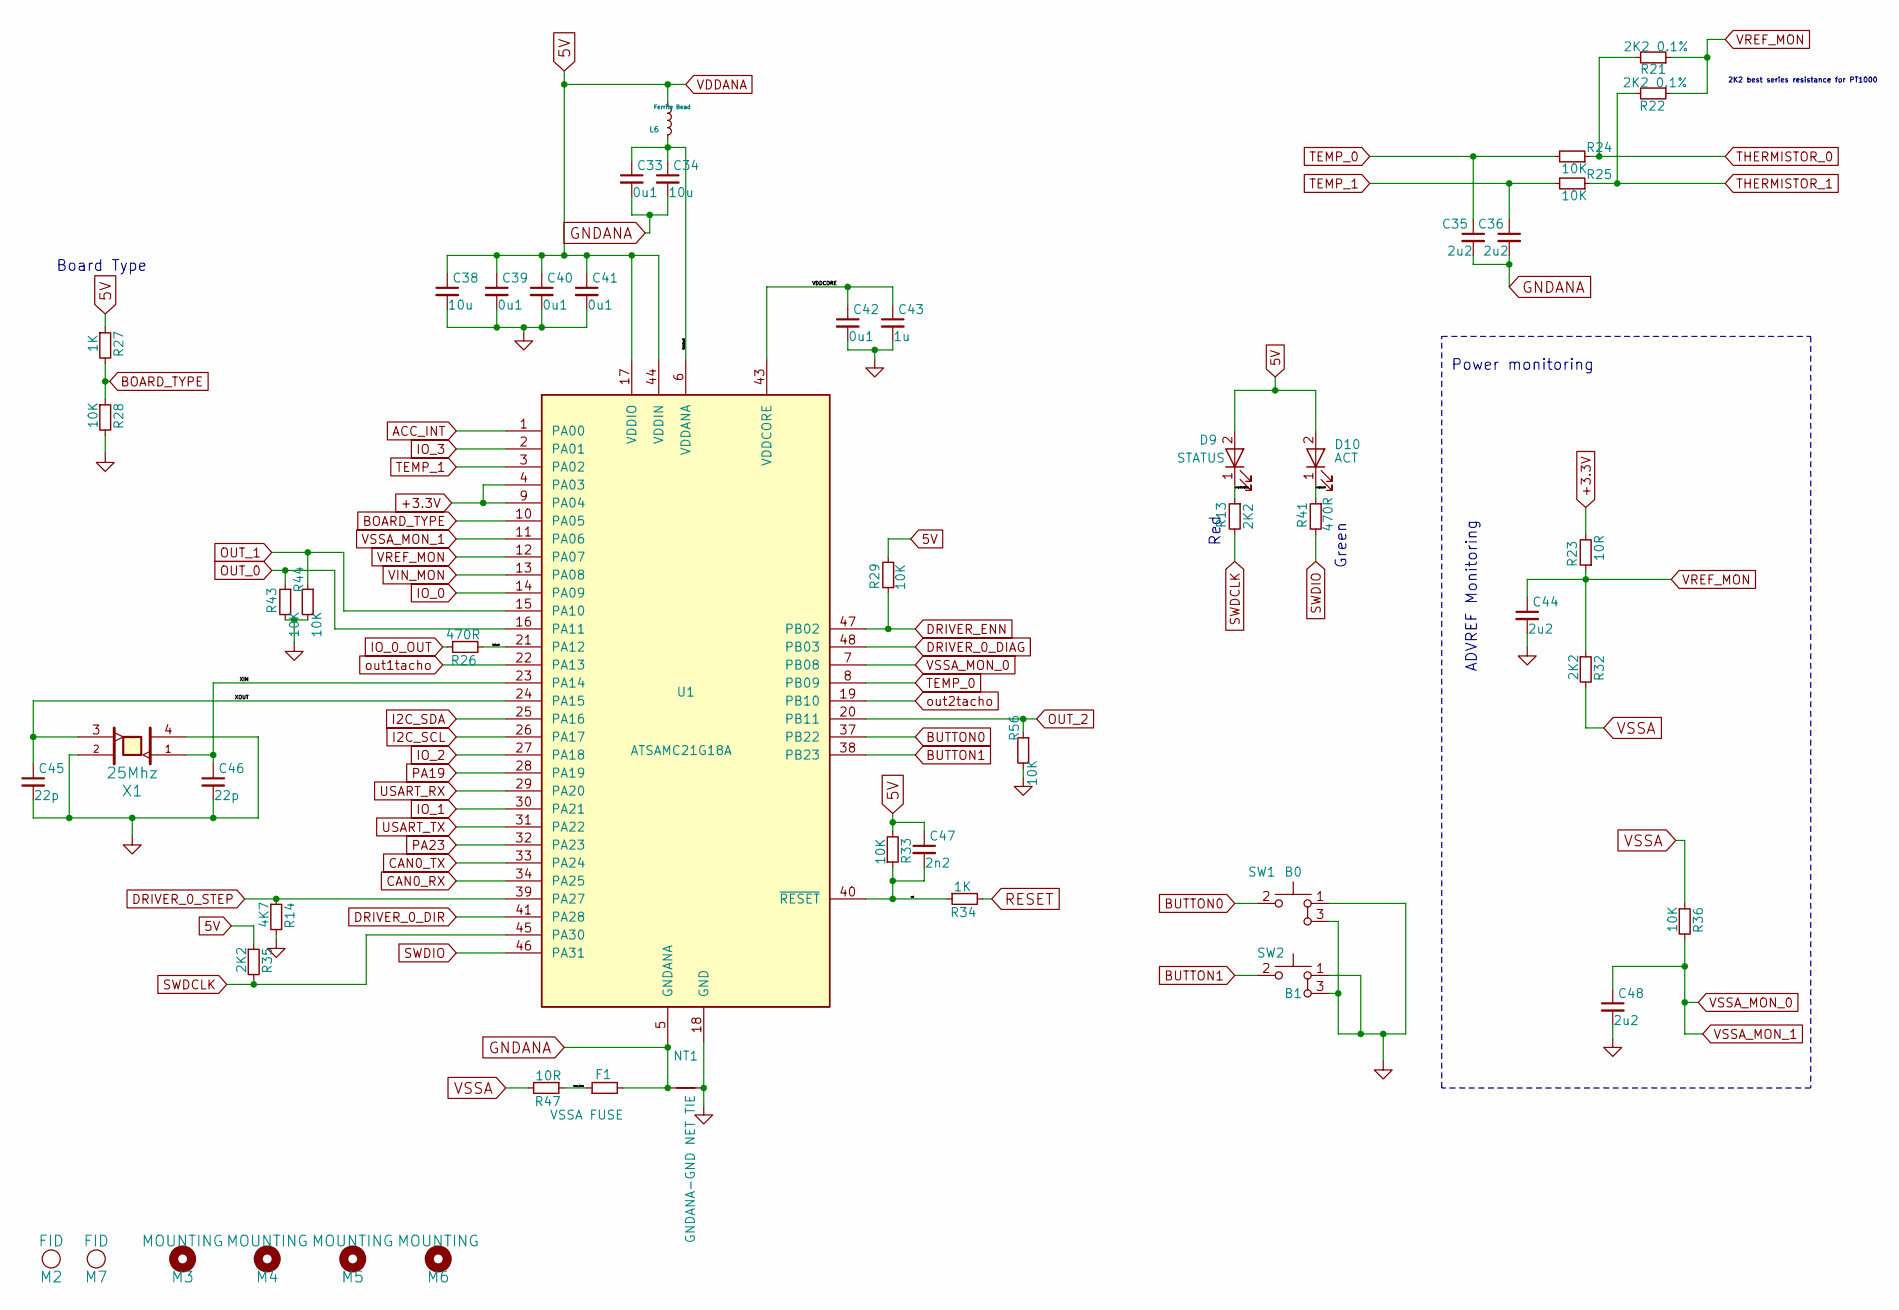
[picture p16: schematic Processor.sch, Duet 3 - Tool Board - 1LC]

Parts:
C33, C39, C40, C41, C42: 0u1; C_0402_1005Metric_Wbry; Part Number CL05A104KA5NNNC
C34, C38: 10u; C_0805_2012Metric; Part Number CL21A106KPFNNNG
C35, C36, C44, C48: 2u2; C_0603_1608Metric_Wbry; Part Number GRM188R6YA225KA12D
C43: 1u; C_0603_1608Metric_Wbry; Part Number CL10A105KA8NNNC
C45, C46: 22p; C_0402_1005Metric_Wbry; Part Number C0402C220J4GACTU
C47: 2n2; C_0402_1005Metric_Wbry; Part Number CC0402KRX7R9BB222 or similar (10v+ is f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
D9: STATUS; LED_0603_1608Metric; Part Number 150060RS75000 or equivalent Red
D10: ACT; LED_0603_1608Metric; Part Number 150060VS75000 or equivalent Green
F1: VSSA FUSE; Fuse_1206_3216Metric; Part Number 0ZCJ0020FF2E
L6: Ferrite Bead; L_0402_1005Metric; Part Number BKP1005HS221-T
M2, M7: FID; Fiducial_1mm_Mask2mm; Part Number virtual component - DNP
M3, M4, M5, M6: MOUNTING; MountingHole_3.2mm_M3; Part Number virtual component - DNP
NT1: GNDANA-GND NET TIE; NetTie-2_SMD_Pad0.5mm; Part Number virtual component - DNP
R13, R32, R35: 2K2; R_0402_1005Metric_Wbry; Part Number RK73H1ETTP2201F
R14: 4K7; R_0402_1005Metric_Wbry; Part Number RK73H1ETTP4701F
R21, R22: 2K2 0.1%; R_0402_1005Metric_Wbry; Part Number RT0402BRE072K2L
R23, R47: 10R; R_0402_1005Metric_Wbry; Part Number RK73H1ETTP10R0F
R24, R25, R29, R33, R36, R43, R44, R56: 10K; R_0402_1005Metric_Wbry; Part Number RK73H1ETTP1002F
R26, R41: 470R; R_0402_1005Metric_Wbry; Part Number RK73H1ETTP4700F
R27: 1K; R_0402_1005Metric_Wbry; Part Number RK73H1ETTP2202F
R28: 10K; R_0402_1005Metric_Wbry; Part Number RK73H1ETTP1001F
R34: 1K; R_0402_1005Metric_Wbry; Part Number RK73H1ETTP1001F
SW1: B0; SW_TL3340AF160QG; Part Number TL3340AF160QG
SW2: B1; SW_TL3340AF160QG; Part Number TL3340AF160QG
U1: ATSAMC21G18A; QFN-48-1EP_7x7mm_P0.5mm_EP5.2x5.2mm_ThermalVias_thinpads; Part Number ATSAMC21G18A
X1: TSX-3225 25.0000MF10P; Crystal_SMD_ECS-33B-4Pin_3.2x2.5mm; Part Number TSX-3225 25.0000MF10P

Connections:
5V: C38.1, C39.1, C40.1, C41.1, C47.1, D9.2 (A), D10.2 (A), L6.1, R27.1, R29.2, R33.2, R35.1, U1.17 (VDDIO), U1.36 (VDDIO), U1.44 (VDDIN); also elsewhere on the board
+3.3V: R23.2, U1.4 (PA03), U1.9 (PA04); also elsewhere on the board
/Processor/VDDANA_IN: C33.1, C34.1, L6.2, U1.6 (VDDANA)
/Processor/VDDCORE: C42.1, C43.1, U1.43 (VDDCORE)
/Processor/XIN: C46.1, U1.23 (PA14), X1.1
/Processor/XOUT: C45.1, U1.24 (PA15), X1.3
/Processor/io0out: R26.2, U1.21 (PA12)
/Processor/rst: C47.2, R33.1, R34.1, U1.40 (~RESET)
/Processor/swdclkstatus: D9.1 (K), R13.1
/Processor/swdioact: D10.1 (K), R41.1
/Processor/vssa_fuse: F1.1, R47.1
ACC_INT: U1.1 (PA00); also elsewhere on the board
BOARD_TYPE: R27.2, R28.1, U1.10 (PA05)
BUTTON0: SW1.2, U1.37 (PB22)
BUTTON1: SW2.2, U1.38 (PB23)
CAN0_RX: U1.34 (PA25); also elsewhere on the board
CAN0_TX: U1.33 (PA24); also elsewhere on the board
DRIVER_0_DIAG: U1.48 (PB03); also elsewhere on the board
DRIVER_0_DIR: U1.41 (PA28); also elsewhere on the board
DRIVER_0_STEP: R14.1, U1.39 (PA27); also elsewhere on the board
DRIVER_ENN: R29.1, U1.47 (PB02); also elsewhere on the board
GND: C38.2, C39.2, C40.2, C41.2, C42.2, C43.2, C44.2, C45.2, C46.2, C48.2, NT1.2, R14.2, R28.2, R43.2, R44.2, R56.2, SW1.1, SW1.3, SW2.1, SW2.3, U1.18 (GND), U1.35 (GND), U1.42 (GND), U1.49 (GND), X1.2, X1.4; also elsewhere on the board
GNDANA: C33.2, C34.2, C35.2, C36.2, F1.2, NT1.1, U1.5 (GNDANA)
I2C_SCL: U1.26 (PA17); also elsewhere on the board
I2C_SDA: U1.25 (PA16); also elsewhere on the board
IO_0: U1.14 (PA09); also elsewhere on the board
IO_0_OUT: R26.1; also elsewhere on the board
IO_1: U1.30 (PA21); also elsewhere on the board
IO_2: U1.27 (PA18); also elsewhere on the board
IO_3: U1.2 (PA01); also elsewhere on the board
OUT_0: R43.1, U1.16 (PA11); also elsewhere on the board
OUT_1: R44.1, U1.15 (PA10); also elsewhere on the board
OUT_2: R56.1, U1.20 (PB11); also elsewhere on the board
PA19: U1.28 (PA19); also elsewhere on the board
PA23: U1.32 (PA23); also elsewhere on the board
RESET: R34.2; also elsewhere on the board
SWDCLK: R13.2, R35.2, U1.45 (PA30); also elsewhere on the board
SWDIO: R41.2, U1.46 (PA31); also elsewhere on the board
TEMP_0: C35.1, R24.2, U1.8 (PB09)
TEMP_1: C36.1, R25.2, U1.3 (PA02)
THERMISTOR_0: R21.2, R24.1; also elsewhere on the board
THERMISTOR_1: R22.2, R25.1; also elsewhere on the board
USART_RX: U1.29 (PA20); also elsewhere on the board
USART_TX: U1.31 (PA22); also elsewhere on the board
VIN_MON: U1.13 (PA08); also elsewhere on the board
VREF_MON: C44.1, R21.1, R22.1, R23.1, R32.1, U1.12 (PA07)
VSSA: R32.2, R36.1, R47.2; also elsewhere on the board
VSSA_MON_0: C48.1, R36.2, U1.7 (PB08), U1.11 (PA06)
out1tacho: U1.22 (PA13); also elsewhere on the board
out2tacho: U1.19 (PB10); also elsewhere on the board

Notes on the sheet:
2K2 best series resistance for PT1000
Power monitoring
Board Type
ADVREF Monitoring
Red
Green

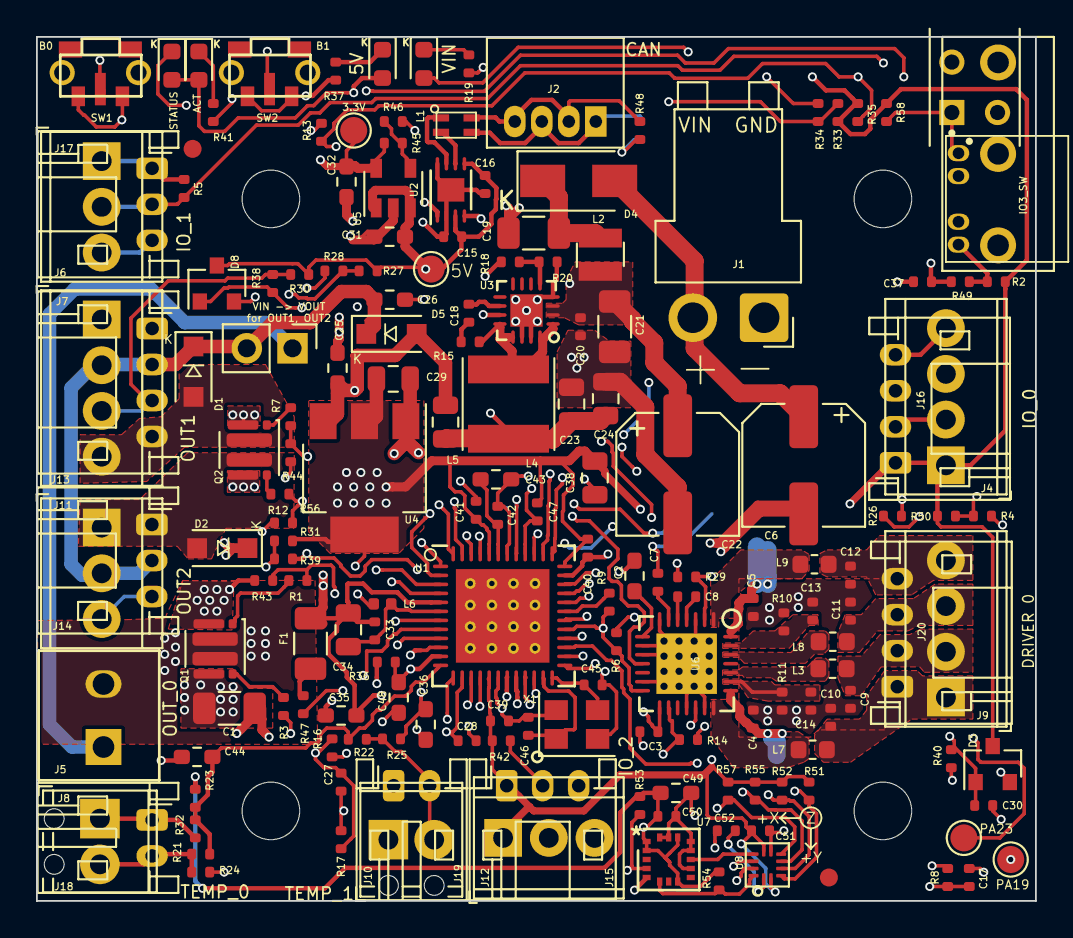
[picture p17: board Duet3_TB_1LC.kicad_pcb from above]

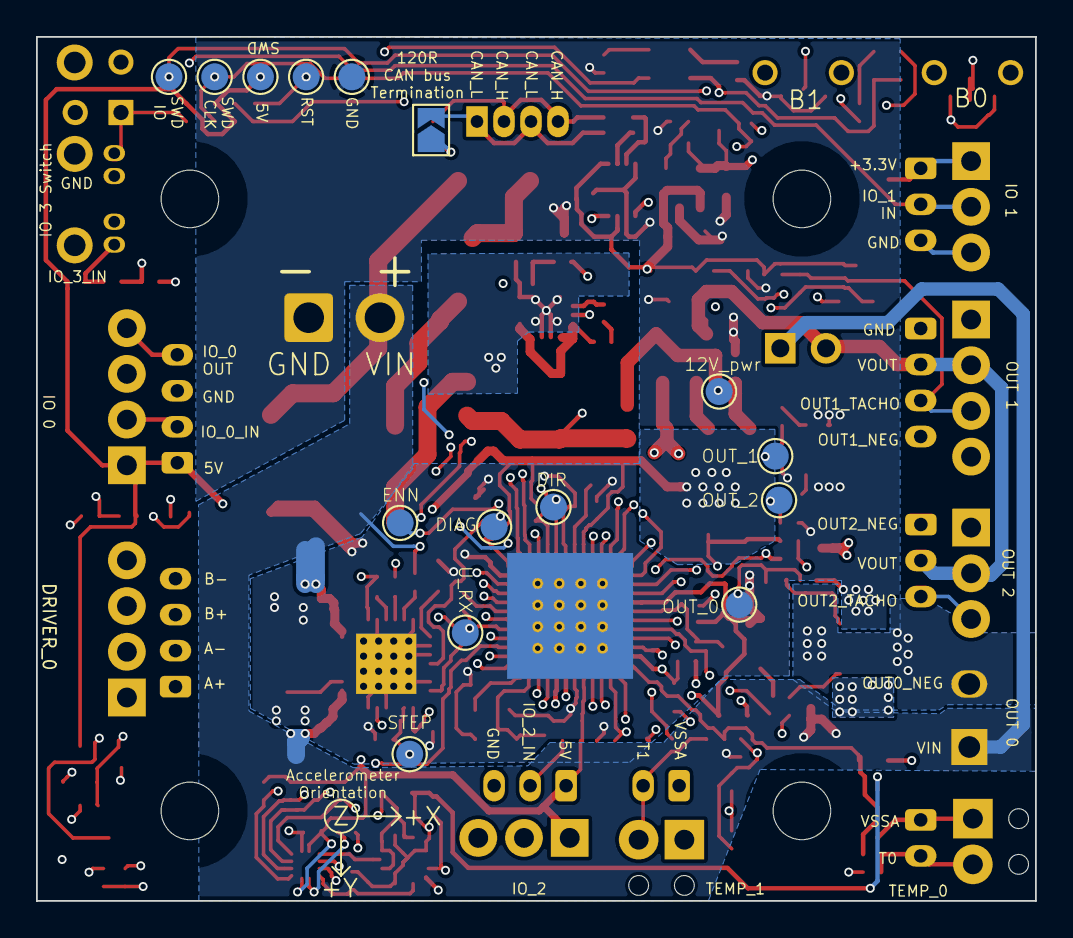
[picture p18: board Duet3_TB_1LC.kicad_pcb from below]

Board: 4 copper layers, 55.5 x 48.0 mm, 192 parts (15 on the bottom side), 100 nets.

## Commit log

2020-02-28 ToolBoard_1LC_v0.6 Schematic and Step file added
2020-06-15 Added wiring and dimension .svgs
2020-06-15 Added Toolboard v1.0 schematic, step and documentation svgs
2021-05-06 Update Duet3_TB_1LC_v1.1_STEP.zip
    Added diode to back of the board
2021-06-23 Added schematic
2021-06-23 Renamed v1.1 schematic
2021-12-21 KiCad files for v0.6
    [Duet3_TB_1LC.kicad_pcb, Duet3_TB_1LC.sch, Headers.sch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]
2021-12-21 KiCad files for v1.0
    [Duet3_TB_1LC.kicad_pcb, Duet3_TB_1LC.sch, Headers.sch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]
2021-12-21 KiCAD files for v1.1
    [Duet3_TB_1LC.kicad_pcb, Duet3_TB_1LC.sch, Headers.sch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]
2021-12-21 Toolboard v1.2 source files.
    [Duet3_TB_1LC.kicad_pcb, Duet3_TB_1LC.sch, Headers.sch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]
2022-05-30 Added iBOM, Schematic and STEP for Toolboard v1.3
